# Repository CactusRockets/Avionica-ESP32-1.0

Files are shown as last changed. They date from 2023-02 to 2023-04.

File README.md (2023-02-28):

A aviônica embarcada foi prototipada e projetada através do software Eagle. Esse projeto inclui as dimensões da placa (PCB), a inclusão dos componentes da aviônica, as relações entre elas e o fornecimento de energia.

Dimensões da placa: 5,6 cm x 12,0 cm

Os materiais incluídos no projeto são:

- 1x PCB
- 1x ESP32 LoRa heltec (V2) + Antena
- 1x MPU6050
- 1X BMP280
- 2x JST de dois pinos (macho e fêmea) (2.54mm)
- 1x Conector microUSB
- 1x Switch (ss12f44g4)
- 1x Módulo SD + Cartão SD
- 1x Pino (PINHD 1X1)
- 2x Baterias de lítio (18650) (3.7V cada)
- 1x Suporte para duas baterias 18650
- Fios de ligação das baterias com o sistema

As trilhas da conexão entre os circuitos foram trilhas de 1mm de largura. A prototipação inclui uma chave de conexão que liga o JST (que se conecta a bateria) ao restante do circuito, para que possa ser feito um acionamento elétrico manual do sistema. Além desses componentes básicos, o projeto da placa inclui também 4x rebites de 2,7mm nas extremidades para fixação da placa.

O CAD está disponível no google Drive da Cactus.

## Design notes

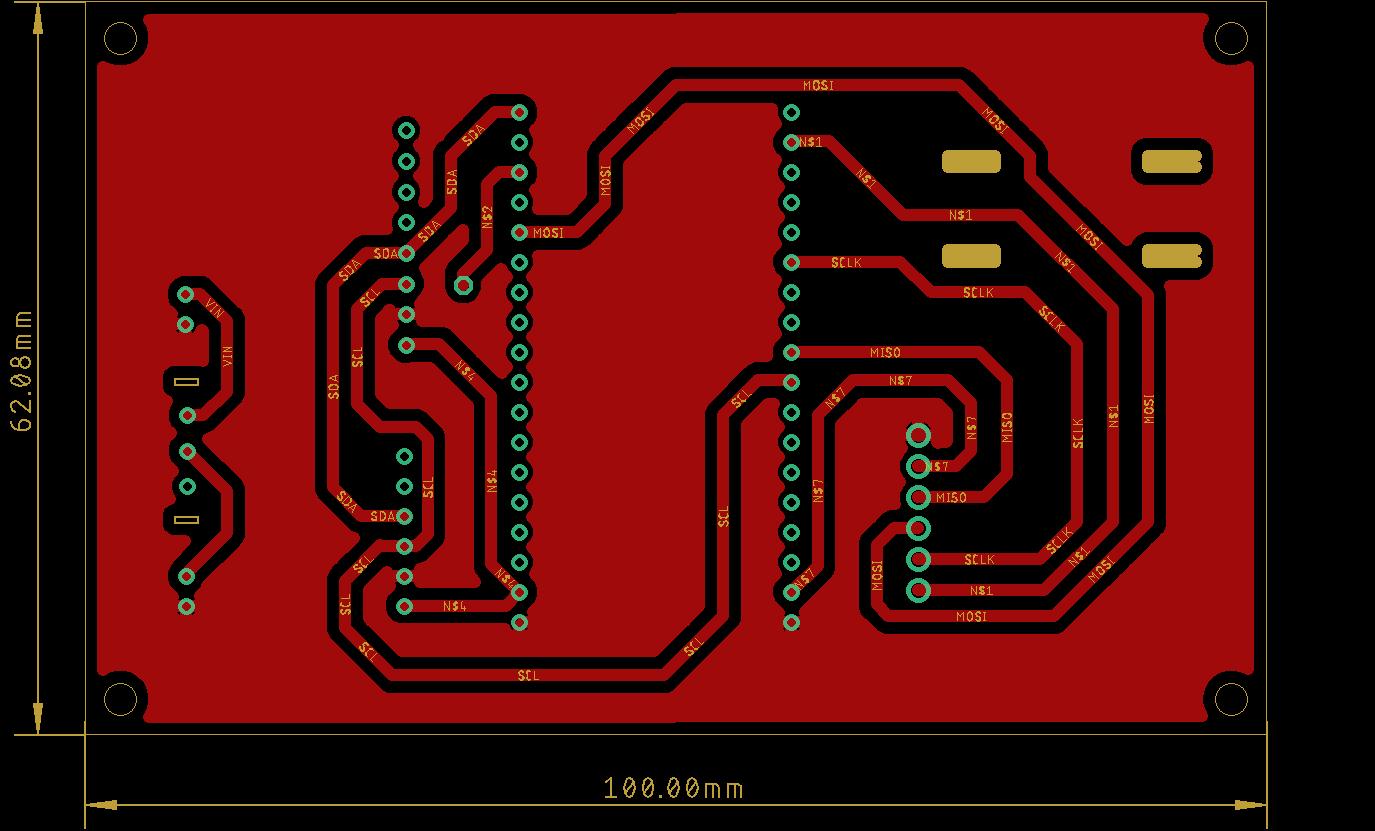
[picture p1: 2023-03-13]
Aviônica/Aviônica 2.0/Avionica.png

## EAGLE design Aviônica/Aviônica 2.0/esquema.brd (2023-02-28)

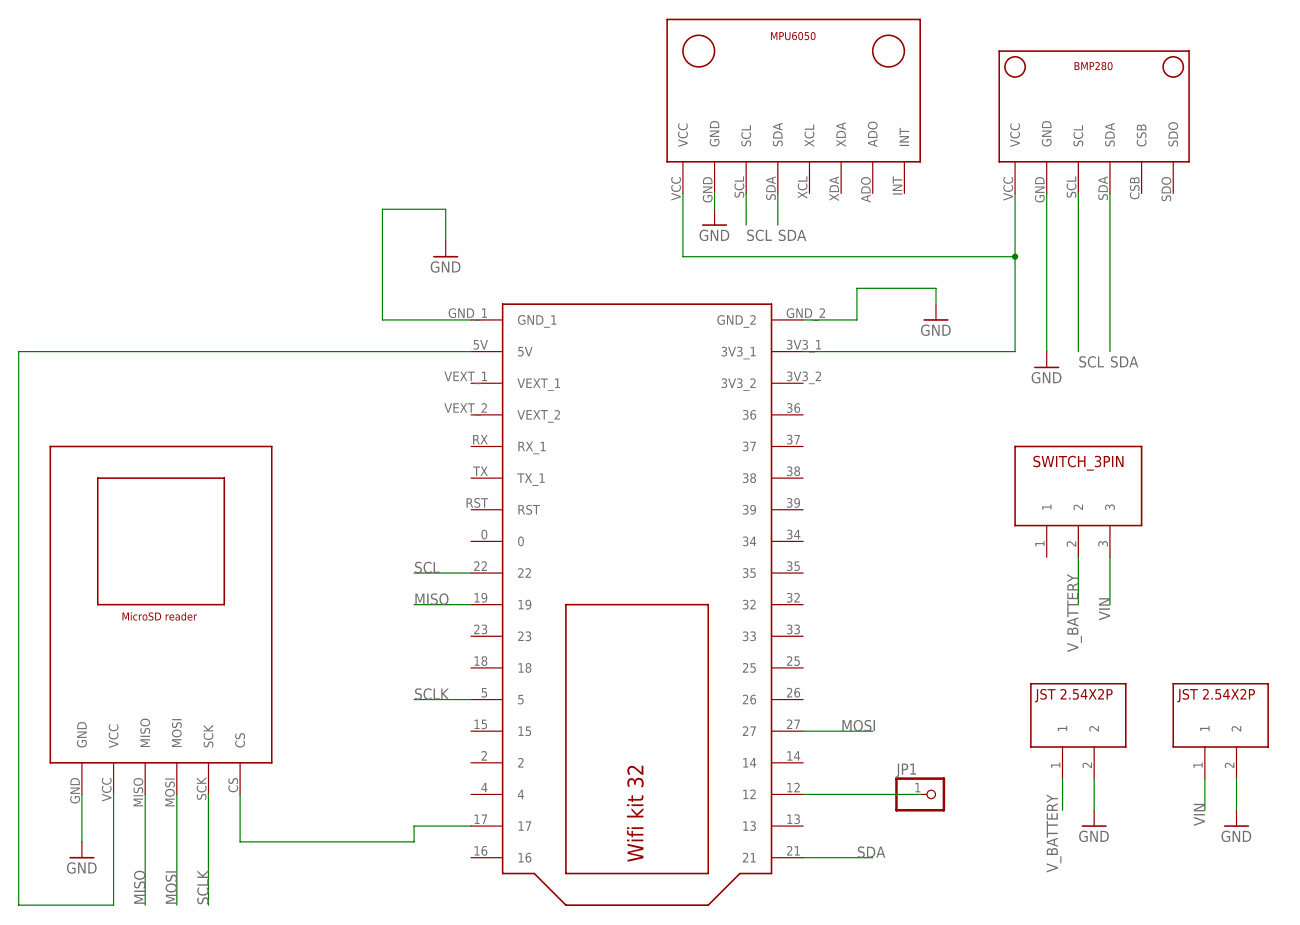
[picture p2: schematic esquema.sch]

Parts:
JP1: PINHD-1X1; 1X01
U$1: BMP280V1; BMP280_FOOTPRINT
U$2: MICROSD_READER; MICROSD_READER_FOOTPRINT
U$3: MPU6050V1; MPU6050_FOOTPRINT
U$4: WIFI_KIT32
U$5, U$7: JST2.54X2P; JST2.54X2P_FOOTPRINT
U$6: SWITCH_3PIN

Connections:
GND: U$1.GND, U$2.GND, U$3.GND, U$4.GND_1, U$4.GND_2, U$5.2, U$7.2
MISO: U$2.MISO, U$4.19
MOSI: U$2.MOSI, U$4.27
unnamed: U$2.CS, U$4.17
unnamed: JP1.1, U$4.12
unnamed: U$1.VCC, U$3.VCC, U$4.3V3_1
unnamed: U$2.VCC, U$4.5V
SCL: U$1.SCL, U$3.SCL, U$4.22
SCLK: U$2.SCK, U$4.5
SDA: U$1.SDA, U$3.SDA, U$4.21
VIN: U$6.3, U$7.1
V_BATTERY: U$5.1, U$6.2

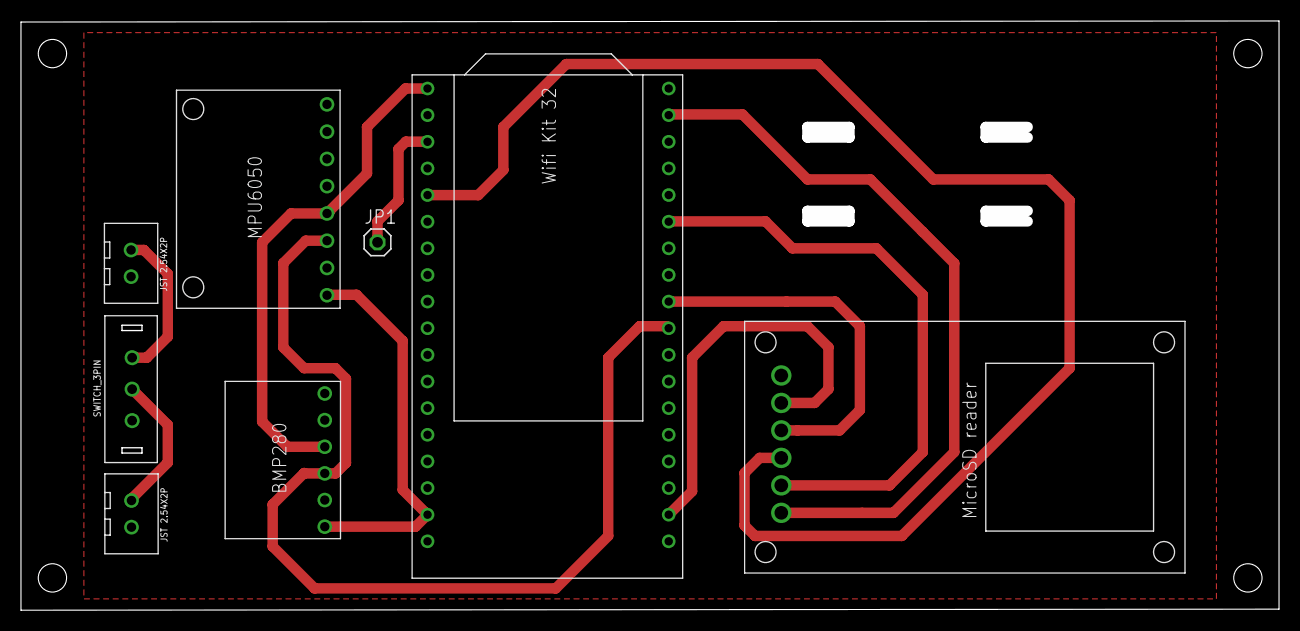
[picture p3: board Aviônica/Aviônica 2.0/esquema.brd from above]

Board: 2 copper layers, 120.0 x 56.2 mm, 8 parts (0 on the bottom side), 12 nets.

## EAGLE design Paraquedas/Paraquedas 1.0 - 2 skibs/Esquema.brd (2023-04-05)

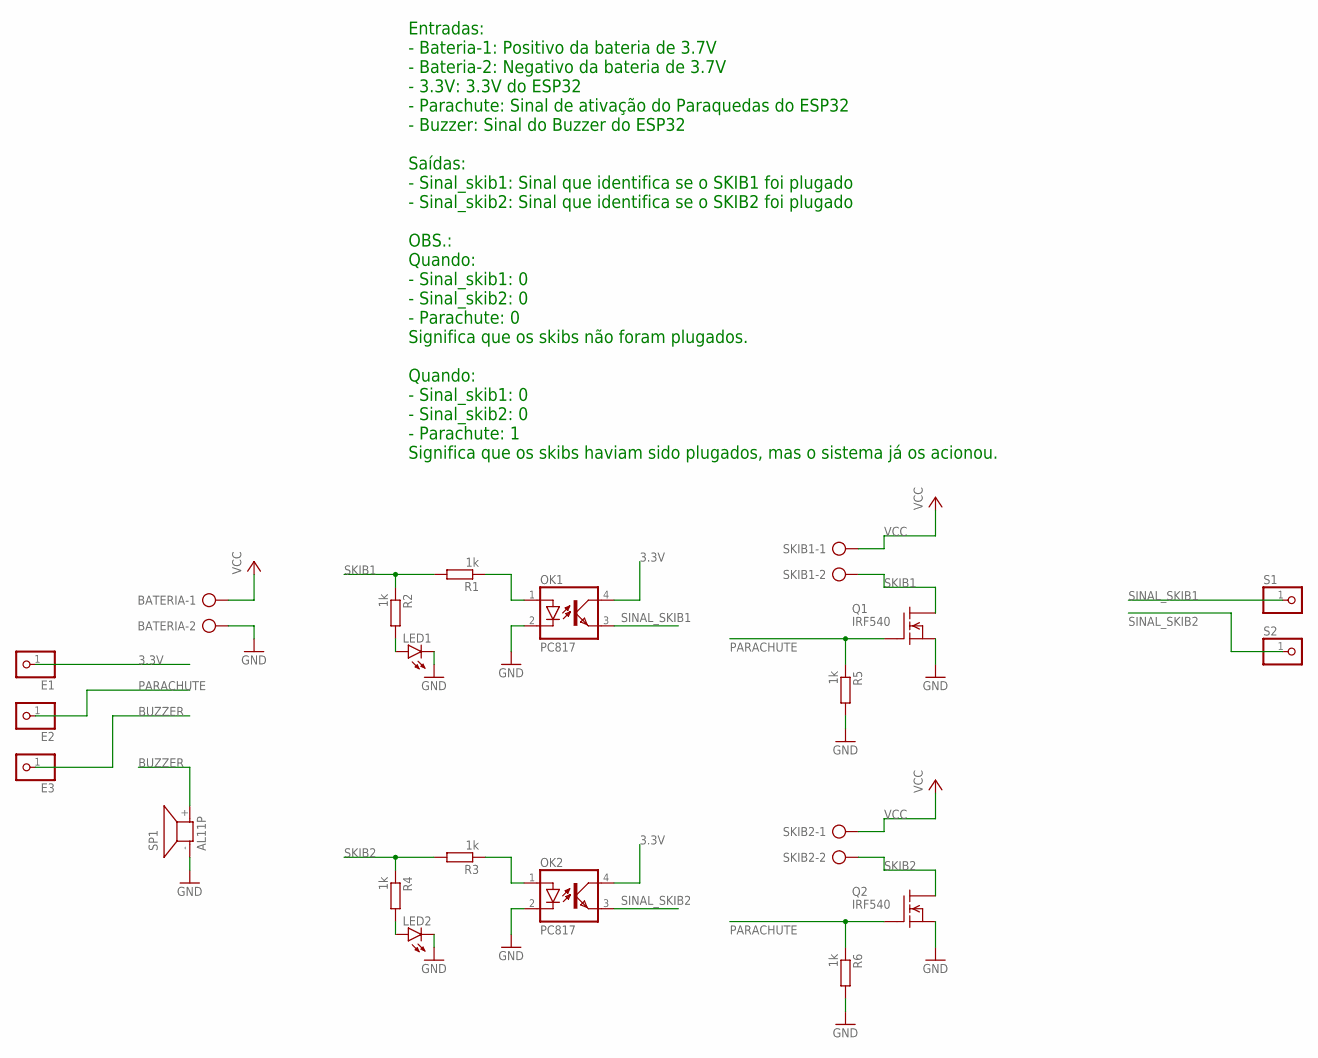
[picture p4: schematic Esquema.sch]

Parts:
BATERIA: AK500/2-H
E1, E2, E3: PINHD-1X1; 1X01
LED1, LED2: LED5MM
OK1, OK2: PC817; DIL04
Q1, Q2: IRF540; TO220
R1, R2, R3, R4, R5, R6: 1k; 0207/10
S1, S2: PINHD-1X1; 1X01
SKIB1, SKIB2: AK500/2-H
SP1: AL11P

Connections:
3.3V: E1.1, OK1.4 (COL), OK2.4 (COL)
BUZZER: E3.1, SP1.+ (2)
GND: BATERIA.2, LED1.K (C), LED2.K (C), OK1.2 (C), OK2.2 (C), Q1.3 (S), Q2.3 (S), R5.2, R6.2, SP1.- (1)
unnamed: OK1.1 (A), R1.1
unnamed: OK2.1 (A), R3.1
unnamed: LED2.A, R4.2
unnamed: LED1.A, R2.2
PARACHUTE: E2.1, Q1.1 (G), Q2.1 (G), R5.1, R6.1
SINAL_SKIB1: OK1.3 (EMIT), S1.1
SINAL_SKIB2: OK2.3 (EMIT), S2.1
SKIB1: Q1.2 (D), R1.2, R2.1, SKIB1.2
SKIB2: Q2.2 (D), R3.2, R4.1, SKIB2.2
VCC: BATERIA.1, SKIB1.1, SKIB2.1

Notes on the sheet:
Entradas: - Bateria-1: Positivo da bateria de 3.7V - Bateria-2: Negativo da bateria de 3.7V - 3.3V: 3.3V do ESP32 - Parachute: Sinal de ativação do Paraquedas do ESP32 - Buzzer: Sinal do Buzzer do ESP32 Saídas: - Sinal_skib1: Sinal que identifica se o SKIB1 foi plugado - Sinal_skib2: Sinal que iden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

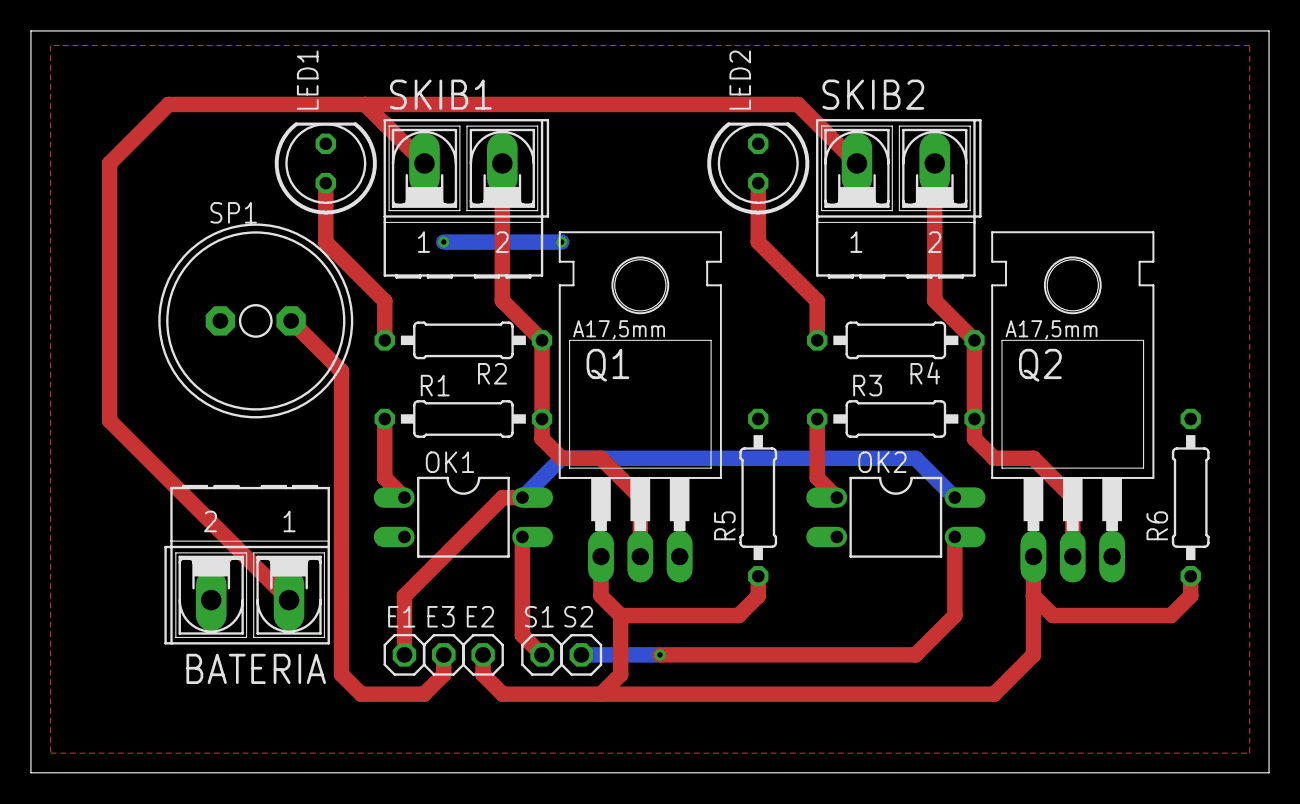
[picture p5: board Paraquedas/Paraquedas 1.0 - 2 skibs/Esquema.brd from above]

Board: 2 copper layers, 80.0 x 47.9 mm, 21 parts (0 on the bottom side), 13 nets.

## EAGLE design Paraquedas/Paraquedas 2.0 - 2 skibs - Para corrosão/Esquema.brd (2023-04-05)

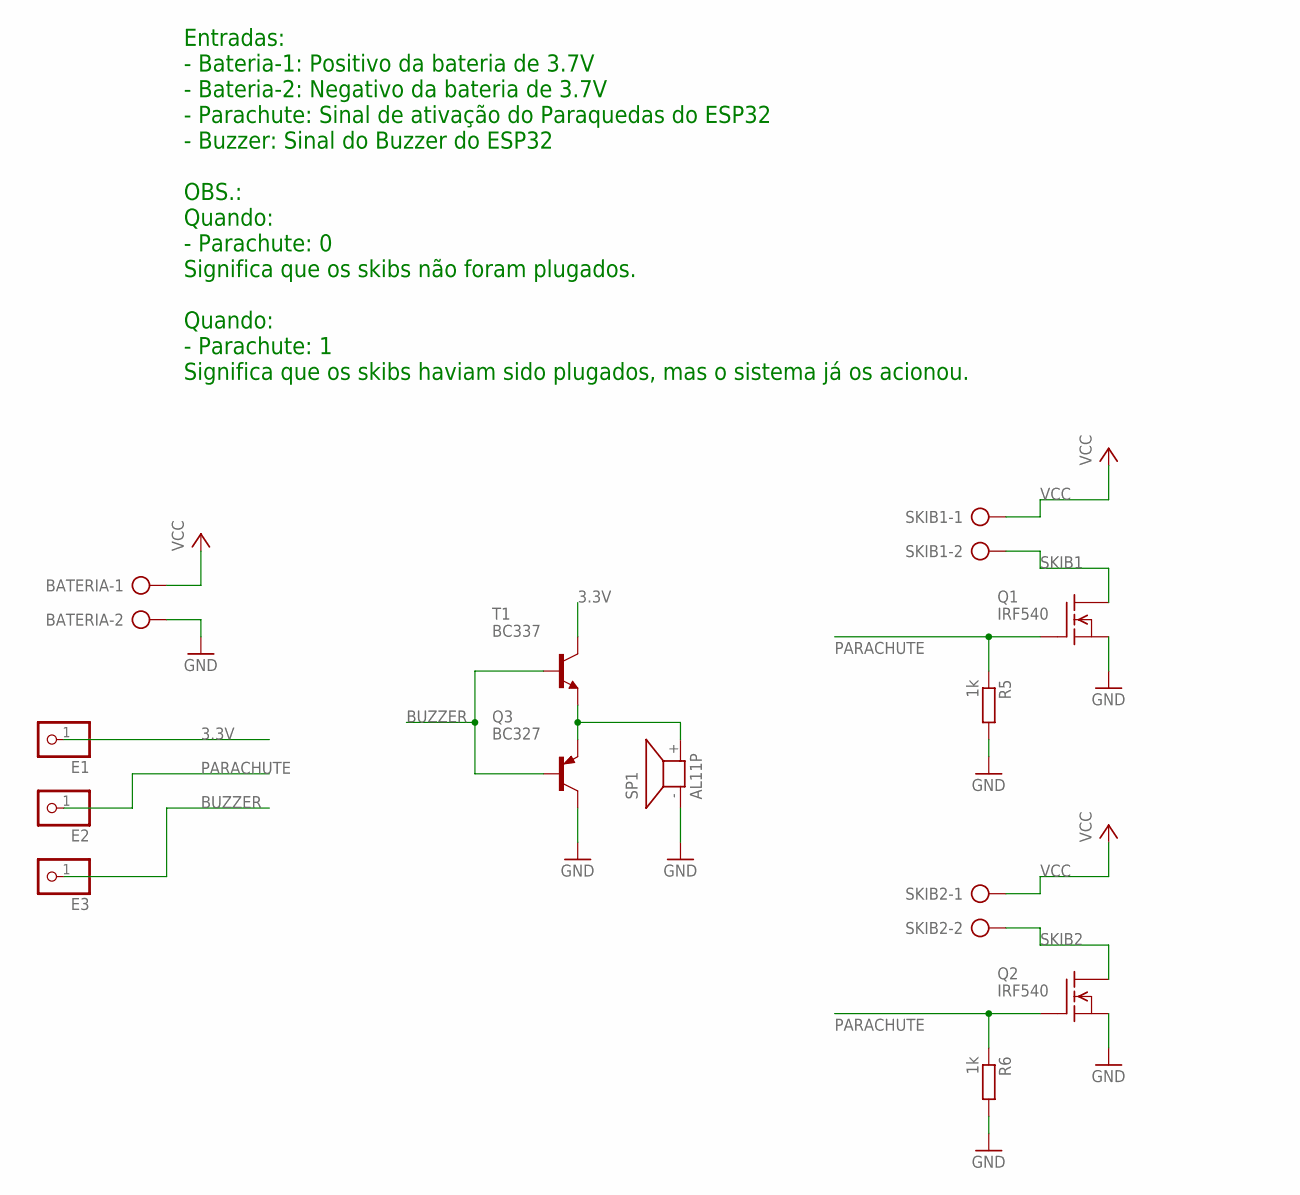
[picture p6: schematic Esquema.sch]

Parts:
BATERIA: AK500/2-H
E1, E2, E3: PINHD-1X1; 1X01
Q1, Q2: IRF540; TO220
Q3: BC327; TO92
R5, R6: 1k; 0207/10
SKIB1, SKIB2: AK500/2-H
SP1: AL11P
T1: BC337; TO92

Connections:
3.3V: E1.1, T1.3 (C)
BUZZER: E3.1, Q3.2 (B), T1.2 (B)
GND: BATERIA.2, Q1.3 (S), Q2.3 (S), Q3.3 (C), R5.2, R6.2, SP1.- (1)
unnamed: Q3.1 (E), SP1.+ (2), T1.1 (E)
PARACHUTE: E2.1, Q1.1 (G), Q2.1 (G), R5.1, R6.1
SKIB1: Q1.2 (D), SKIB1.2
SKIB2: Q2.2 (D), SKIB2.2
VCC: BATERIA.1, SKIB1.1, SKIB2.1

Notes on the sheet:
Entradas: - Bateria-1: Positivo da bateria de 3.7V - Bateria-2: Negativo da bateria de 3.7V - Parachute: Sinal de ativação do Paraquedas do ESP32 - Buzzer: Sinal do Buzzer do ESP32 OBS.: Quando: - Parachute: 0 Significa que os skibs não foram plugados. Quando: - Parachute: 1 Significa que os skibs 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

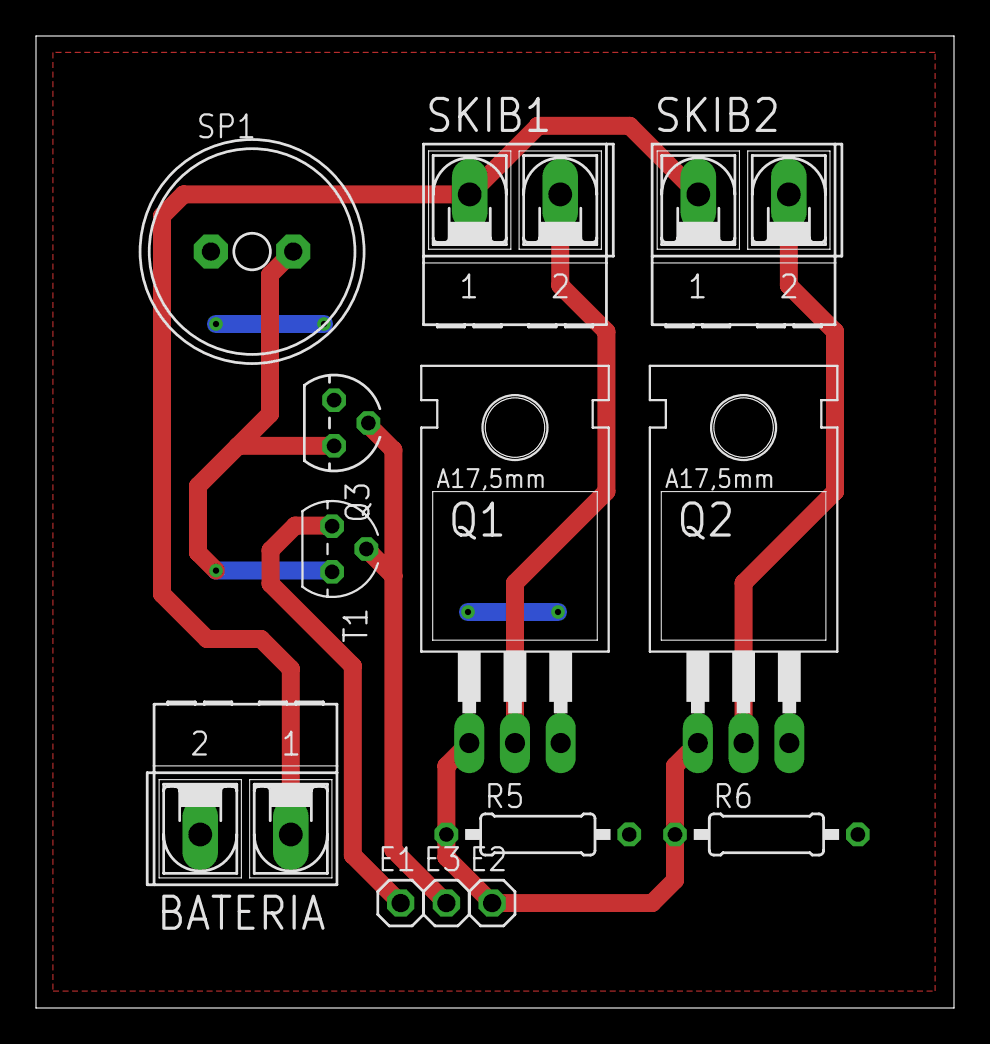
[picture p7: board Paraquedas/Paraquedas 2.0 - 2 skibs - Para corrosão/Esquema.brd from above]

Board: 2 copper layers, 51.0 x 54.0 mm, 13 parts (0 on the bottom side), 8 nets.

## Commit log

2023-03-22 Placa do paraquedas
    [Esquema.brd, Esquema.sch, esquema.brd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]
2023-04-05 Atualização
    [Esquema.brd, Esquema.sch, esquema.brd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]
